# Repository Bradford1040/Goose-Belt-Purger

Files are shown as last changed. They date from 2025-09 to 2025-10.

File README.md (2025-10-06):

# Goose Belt Purger (GBP)
A simple, lightweight, and low-cost belt purger for 3D printers.\
An alternative to blob-producing purging routines and devices, or traditional purging into towers.\
Officially supported printers are Voron Trident and 2.4, but it is small and light enough to be adapted for other printers.

   
  
See also our [promo video](https://youtu.be/ZBZhAEFlKdA) on YouTube, or slightly older [video](https://youtu.be/MWTFuGqhi_c) with more detailed depiction of purger in action.
  
Currently in Beta testing — proven as a functional design, but can have unexpected issues and design might change any time.  
  
If you have any questions, you can visit my [Discord server](https://discord.gg/8a29q9gJb9).  
  
If you find this useful, a like or a make on [Printables](https://www.printables.com/model/1371713-goose-belt-purger-gbp) helps others discover and trust the design.

# About
Like many makers, I've been fascinated by single-nozzle multicolor/multimaterial printing. But like many, I hate purge towers. They can be large, ugly, and take up valuable print bed space. This is why I was intrigued by the Blobifier — but there are several issues. First, I use a Voron Trident, which isn't compatible. While there are adaptations of the Blobifier concept for the Trident, none have gained significant traction. Second, both the original Blobifier and its Trident adaptations generally share the drawback that each purge requires toolhead parking near the bed edge, blocking part of the bed and potentially risking collisions. Third, the produced blobs are volumetrically inefficient. Even though the blobs are relatively compact, their shape means they can't utilize the waste bin space effectively. This is even worse with the loose coil "poops" produced by some printers.

There had to be a better way.

And then it struck me — use a belt to produce compact "line" purges. To be fair, this isn't an entirely new idea. There have been mods involving purging on stationary aluminum platforms or kinematic belts, but none of those options felt right. I wanted something simple, affordable, and buildable from stuff you already have lying around your workshop.\
This is why the Goose Belt Purger was created.

What does it have to do with geese? Nothing. I just like geese.

# Design

The core of the GBP is a silicone wristband — the kind you can get anywhere, often for free. The most common size, which GBP is designed around, is 12 mm wide and 20 cm in circumference. You can use any similar band, even ones with embossing or printing, since we'll use the smooth inner surface. Changing the belt is easy, so use whatever you have and swap it later if needed.

Silicone rubber is ideal for this use. When filament is extruded onto the smooth side, it sticks but releases easily at the end of the straight belt section. Silicone is heat-resistant enough to endure the nozzle heat, provided it keeps moving. However, if the nozzle stays in one place too long, the band will discolor (brown or black) or even burn.

The belt moves along two printed pulleys. How does it stay in place without flanges? Dark magic. Don't ask.

One pulley is driven by a cheap miniature DC motor with a gearbox.  A 50rpm or slower version is recommended, up to 15rpm if you want really thick extrusions. &#x20;

> [!WARNING]\
> Motor is an inductive component. Skipping the recommended protection (e.g. flyback diode) can cause voltage spikes and permanent damage to your controller.  
>  
>Read the “Electrical connection” section and install all safety components.  
>Use at your own risk.  

The other pulley spins freely on a tilting arm. The arm pivots on a bearing around the motor shaft and is pushed upward by a pair of magnets acting as springs. The arm's purpose is to press against the nozzle but move away to avoid collisions with the nozzle or printhead.

GBP is mounted using an Armored Turtle brush mount or universal Klicky style mount. But you can also design your own mount and connect it with AT mount styled dovetails.

# Bill of Materials (BOM)
## Purger
- 1x Silicone wristband (12 mm wide, 200 mm circumference)
- 1x DC motor, 12 mm diameter, 6V/12V, 15rpm — commonly sold as GA12 N20 or N30. See note below.
- 3x 623 bearings
- 2x 6x3 mm magnets (Voron standard size)
- 3x heat-set insert M3x5x4 (Voron standard size)
  
If your board supports 5V on fan outputs, you may use a 6V motor. If only 24V is available, use a 12V motor with <50% PWM.  
Initial testing shows optimal belt speed under load is 2–12rpm, so the 15rpm seems to be ok. PWM can reduce speed to \~5–10% of rated speed. 30rpm and 50rpm motors also seem to be usable  

**M3 hardware:**

- 1x M3 nut
- 1x M3 nylock nut*
- 1x M3x6 set screw
- 1x M3x20 SHCS*
- 2x M3x20 FHCS
- 1x M3x30 SHCS
  
*) If you have trouble getting a M3 nyloc, you can instead use HSI variant of arm - replace nylock nut for one more heat-set insert, M3x16 SHCS instead of M3x20 SHCS and get some threadlocker  

**Electrical components:**
- Schottky diode 1A (e.g. 1N5819) - For 5V or 12V supply voltage  
or
- Schottky diode 2A (e.g. 1N5820) - For 24V supply voltage together with 12V motor  
- Resistor 47R
- Ceramic capacitor 10 nF, 50V 
  
If you don't like the idea of soldering those parts, you can also get yourself a **[MicroFlip](https://github.com/Trondle-Embeeded-Systems/MicroFlip)** board, which already has everything.

## Mounts
**AT mount**  
Applies to Voron Trident or similar printer together with modified (shorter) AT mount files  
- 2x heat-set insert M3x5x4 (Voron standard size)
- 2x M3 nyloc nut
- 2x M3x8 SHCS
- 1x M3x35 SHCS (you can use M3x30 if you have trouble getting it)
- 1x M3x25 SHCS

**Klicky style mount**  
Universal solution  
- 8x heat-set insert M3x5x4 (Voron standard size)
- 8x M3x8 SHCS

# Build Instructions

Build instructions can be found [here](assembly.md).

# Electrical Connection

Connect the DC motor to any free power output on your controller board, preferably a fan output. If possible, supply it with 5V or 12V to minimize heating. Otherwise, reduce voltage via PWM.

> [!IMPORTANT]\
> The DC motor is a strong inductive load and will generate large voltage spikes, which can destroy your board's MOSFET or even the MCU if untreated. At minimum, use a properly sized Schottky flyback diode across the board output. I also recommend an RC snubber on the motor terminals.
>
> Some boards (e.g., BTT Octopus) already include protection diodes. Others rely only on the MOSFET's internal diode, which is usually insufficient. You can check comprehensive table [here](board_list.md), or consult your board's schematic.  When unsure, ask someone.
>
> For the RC snubber, I used a 47 Ω resistor and a 10 nF, 50V ceramic capacitor. Solder one leg of each component together, then solder the free legs to the motor terminals. This configuration dampens voltage spikes while preserving PWM response. You may use a larger capacitor for extra safety, but note that increased capacitance degrades PWM response. Avoid using a capacitor alone (without resistor), as this can cause resonance and make things worse.

I confirmed the effectiveness of these measures with an oscilloscope, but I can't guarantee that no fast transients were missed (e.g., during PWM changes). Data is still limited, so proceed with care and understand what you're doing.

If you want some better alternative to manually soldering components to motor, see amazing [MicroFlip](https://github.com/Trondle-Embeeded-Systems/MicroFlip) project by Ntrondle. You can make it yourself, or check our Discord if anyone has any boards for sale. Keep in mind, that MicroFlip is **not** developed as part of this project. If you like it and would like to support its creator, do so on his GitHub page.  

# Software and Slicer Configuration
For more information about provided configuration file, slicer configuration and integration into AFC or Happy Hare, please look [here](sw_configuration.md).

# Tips and Observations
 
Extrude onto the smooth inner side of the wristband. You can try the outer side, but adhesion is generally worse and requires an unembossed, unprinted band — which is surprisingly hard to find. The inner surface sticks well, even without direct nozzle contact, while the outer side requires pressure that magnets alone can't provide.

Adhesion heavily depends on belt speed. If filament doesn't stick, slow the belt. Once adhesion starts, the extruded line tends to pull more material from the nozzle. 
  
Adhesion is also strongly dependant on filament drynes. Wet filament tends to curl up and does not stick to belt as easilly.

The macro splits the purge into short "toothpicks" or pellets to improve waste volume efficiency.

Initial testing shows optimal belt speed is 2–12rpm (roughly 1.8–11 mm/s or 108–660 mm/min). The easiest way to measure speed is to mark a spot on a pulley, start a stopwatch, and time 10 full revolutions.

Don't be afraid to experiment with the macro parameters. Every printer is unique, so expect to tune it up for a some time untill you hit the 'just right' zone.

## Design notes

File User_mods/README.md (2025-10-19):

#Goose Belt Purger - User mods
Files in this folder are user mods related to the Goose Belt Purger. Although they have been curated by me (Graylag) and have been confirmed to meet certain minimum standards, they are not considered a core part of the project and are neither developed nor maintaned by the GBP team.  
All credit goes to the original authors of these mods. If you have any questions or ideas, please try to contact the original authors. Our Discord server might be an ideal place to do that.  
  
Would you like to have your mod here? Contact me on Discord (username graylag) or send me an email. I reserve the right to not publish every submission, but if your work meets minimum qzality requirements and can be helpful to someone, I will try to publish it.  

##List of the user mods

Dragi2k's alternative V2.4 mount - by Dragi2k

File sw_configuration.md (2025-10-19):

# Configuration file and macro configuration
Applies to configuration file v0.7.1 or newer. If you have any kind of issues, check first, if you are on newest available version.

## Instalation of macro into Klipper
Copy the `goose_belt.cfg` file into Klipper configuration file and add `[include goose_belt.cfg]` into your `printer.cfg`. No additional steps are needed

## Macro configuration
Macro can be configured by changing its user accessible variables. See comments in the file and adapt it to your printer.  

Once set up, the purge routine can be triggered by running the G-code macro:  
 - `GOOSE_PURGE PURGE_VOLUME=###`  
   or  
 - `GOOSE_PURGE PURGE_LENGTH=###`  
where ### is the purge volume in mm³ or length in mm. If both are provided, PURGE_LENGTH takes precedence. If neither is provided, the macro runs according default value variable configured within the macro.

## Useful tips
Tuning the variables "just right" can take many iterations and hitting that Save&Restart button every time can be very time consuming. Instead, you can edit your variables on the fly through terminal command `SET_GCODE_VARIABLE`, e.g. `SET_GCODE_VARIABLE MACRO=goose_purge VARIABLE=belt_pwm VALUE=0.33` to change the belt speed. You can even do that during print job - set up a test print that has a bunch of filament changes, then adjusted the variables live as you go. Because the way klipper queues up gocode, it may not take effect immediately so if you enter this while you're in the middle of a toolchange, you won't see the results until the next toolchange.  
Keep in mind this doesn't save the values to config file, so you will have to remember to set the values in the cfg file yourself. 

## GBP and other printer firmwares
No other printer firmwares are supported as of this moment. We are open to add support for other firmwares if you are interested, however be prepared to provide extensive support for a development for your choosen platform.

# Integration of Goose Belt Purger into your print jobs

## Standalone operation (Slicer controlled)
You can use GBP in standalone mode independently on any other klipper add-ons. You can even use it this way if you don't have any MMU/AMS on your printer, e.g. for manual filament changes. Purging can be triggered manualy, or more commonly by slicer.  

Slicer configuration is following:  
For initial priming, place the `GOOSE_PURGE` command with appropriate parameter at the beginning of your **Start G-code** where you'd normally place a prime line.  
For tool changes, insert the command into **Tool change G-code** just after the `T#` command.  
Note that not all slicers support passing purge parameters. In OrcaSlicer, you can use `GOOSE_PURGE PURGE_LENGTH=[flush_length]`. In PrusaSlicer, the volume must be hardcoded.  For other slicers, consult their documentation. 

If you are using GBP in standalone mode but let filament changes handling to Happy Hare or a similar tool, configure it so it doesn't return toolhead to the previous or next G-code position to avoid unnecessary travel.  

## AFC integration 
*Contributed in full by adamcstorm*  
To integrate with AFC-Klipper-Add-On:  

Modify `AFC.cfg`. Under the Macro Config section, change the poop settings to use the goose_purge macro, and disable the kick option:  
```
# Poop Settings
poop: True                      # Enable Poop.
poop_cmd: GOOSE_PURGE           # Poop macro name.

# Kick Settings
kick: False                     # Enable Kick.
kick_cmd: AFC_KICK              # Kick macro name.
```
All other settings can be enabled/disabled per your preference.  
Of note, if you have wipe enabled, the wipe routine will be called twice. This is due to the default AFC order of operation that wipes both before and after the kick routine. Since we have disabled the kick routine, it performs the wipe twice in a row. It is recommended to disable the wipe option in `AFC.cfg`, and instead call the brush routine within the `goose_purge` macro by modifying the user_end_script variable: `variable_user_end_script: 'AFC_BRUSH'`.

GBP is compatible with the default AFC method of passing the variable purge length from the slicer to the print via gcode. To configue this, follow this guide:  
https://www.armoredturtle.xyz/docs/afc-klipper-add-on/features.html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.  
Be aware, that the GBP macro does not access the AFC variables and as such ignores the AFC's variable `variable_purge_lenght`. Instead you should configure GBP's own variable `variable_default_purge_volume`. This value gets used only when no purge parameters are provided, such as during initial load. 

## Happy Hare integration
Happy Hare takes rather complex approach to purging. Unlike other methods it does not rely on slicer to pass purge volume or length together with toolchange. Instead it works with internal purge volume matrix and further enhances it by adding volume of residual filament and cut tip fragment. It can get its purge volume matrix either from internal toolmap or from processing gcode metadata. Either way, for purging to work you need to make sure, that your instance of Happy Hare processes this data correctly. For more information, please visit Happy Hare documentation here:  
https://github.com/moggieuk/Happy-Hare/wiki/Tip-Forming-and-Purging

Also please note, that even if your Happy Hare is configured correctly, it relies on slicer to pass the purging matrix correctly. While this assumption seems to be met for Prusa Slicer, it does not seem so for Orca Slicer. If you use Orca Slicer, consider generating purge volume matrix from toolmap, using custom purge volume matrix or operating GBP in standalone mode.  

As for actual integration, this is very straightforward and the only thing you need to do is edit `mmu_macro_vars.cfg` by setting variable `variable_user_post_load_extension : '_GOOSE_PURGE_HH'` without any parameters.   
  
Note, that we are not calling directly `GOOSE_PURGE` macro, but instead its wrapper `_GOOSE_PURGE_HH`. This is due to how Klipper resolves macros and passes parameters.
  
Happy Hare does not have any wiping logic embedded, so if you want automatic wiping execution after purge, consider adding your custom wiping macro to the `variable_user_end_script:''` in `goose_belt.cfg`.

## Other filament management add-ons
No other filament management add-ons are supported as of this moment. You are free to develop integration into other add-ons and if you do, we can list them here, however be prepared to support such solution.

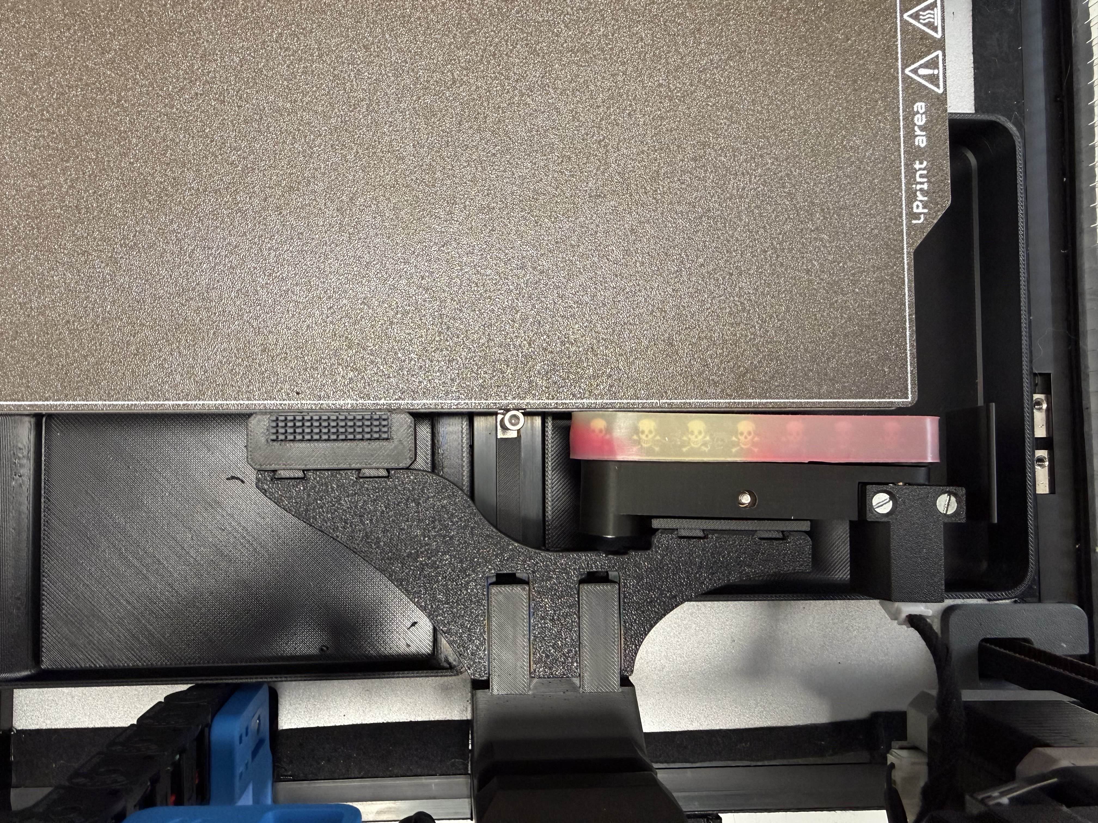
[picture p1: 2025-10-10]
Assets/V2.4/image.jpg

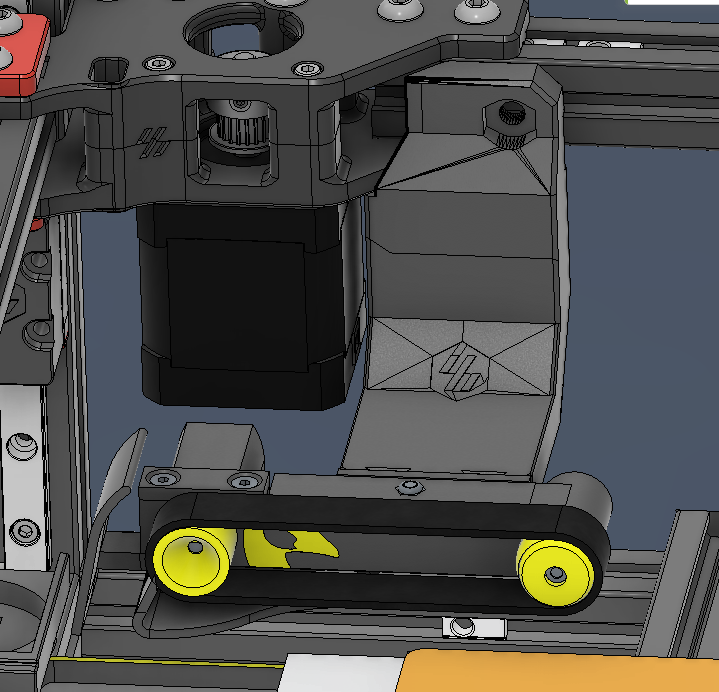
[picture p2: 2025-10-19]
User_mods/Dragi2ks_alternative_v2.4_mount_-_by_Dragi2k/image.png

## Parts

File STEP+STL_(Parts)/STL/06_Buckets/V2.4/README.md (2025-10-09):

Center - to be placed in between bed profiles. It is supposed to catch debris from the brush  
  
Front access - Bucket shaped in such way, that it can be slid under the bed all the way to the front and pulled out of printer. 
Can be removed without lifting the gantry, but does not have locking mechanism to frame. You can either leave it loose, or you can secure it with self adhesive velcro.

Rear access - Bucked designed to be removed by moving it towards back and lifting it along rear panel. Has locking to frame by clips, but requires to lift gantry high up before emptying.

Center bucket and Front access buckets were designed by AmfKuna

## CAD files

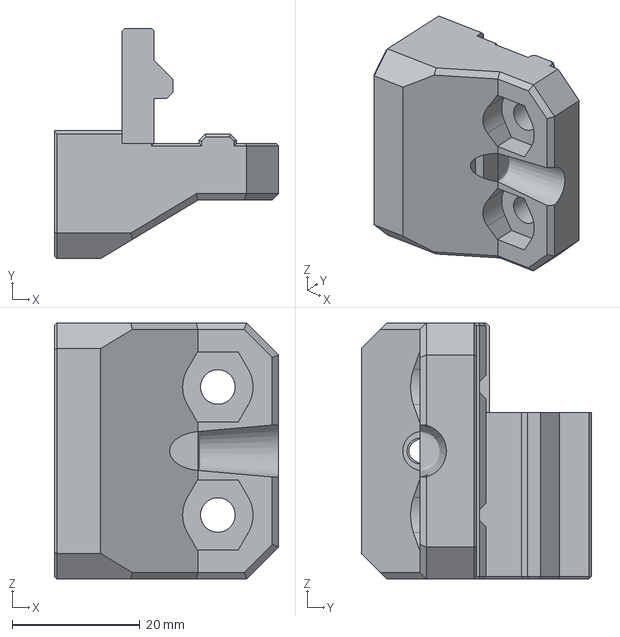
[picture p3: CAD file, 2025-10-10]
STEP+STL_(Parts)/STEP/01_Mounts/AT_Style-Voron_Trident+2.4/ATmount_upper_(GBP).step
35.0 x 36.0 x 40.0 mm

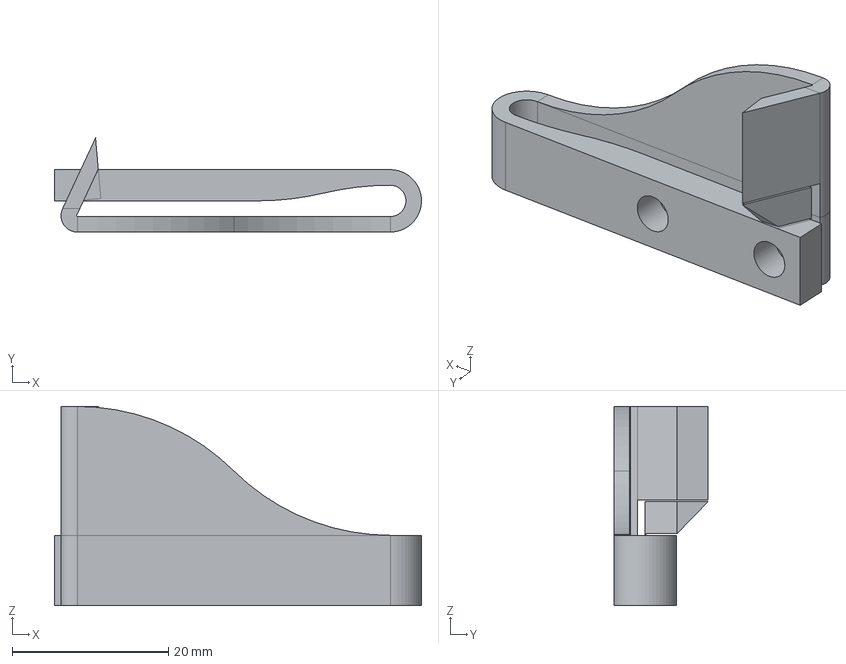
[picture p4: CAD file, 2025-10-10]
STEP+STL_(Parts)/STEP/02_Alternative_parts/GBP_Deflector_lite.step
47.0 x 12.1 x 25.5 mm

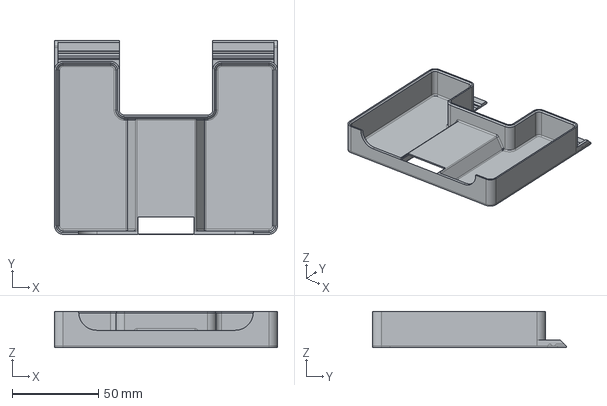
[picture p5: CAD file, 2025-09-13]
STEP+STL_(Parts)/STEP/04_Buckets/bucket_V2.4-central.step
129.0 x 112.0 x 21.0 mm

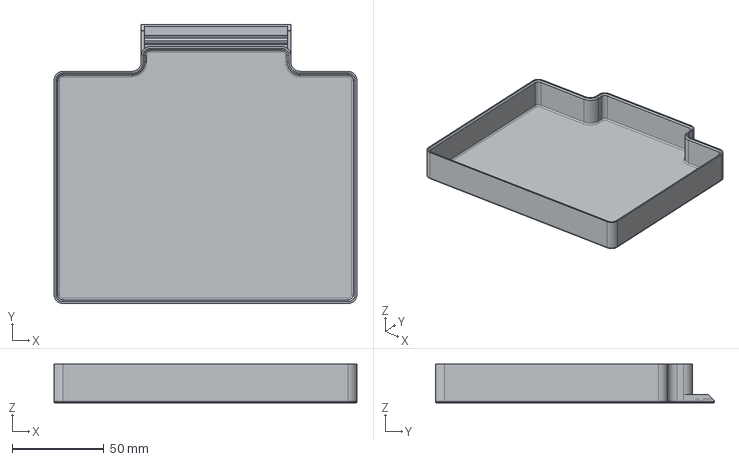
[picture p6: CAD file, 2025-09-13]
STEP+STL_(Parts)/STEP/06_Buckets/Trident/bucket_Trident-300.step
165.0 x 152.0 x 21.0 mm

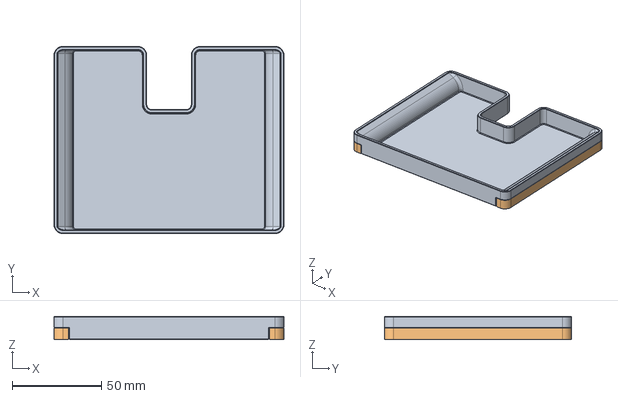
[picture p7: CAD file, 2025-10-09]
STEP+STL_(Parts)/STEP/06_Buckets/V2.4/V2.4_Center/GBP_V2.4-center_bucket.step
129.0 x 105.0 x 13.0 mm

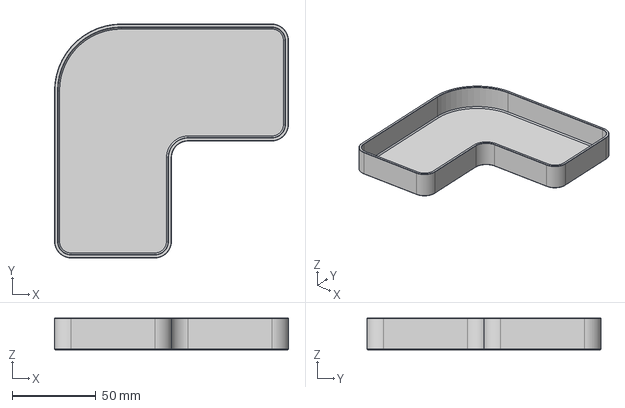
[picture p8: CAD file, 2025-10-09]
STEP+STL_(Parts)/STEP/06_Buckets/V2.4/V2.4_Front_access/GBP_bucket_V2.4-300.step
140.0 x 140.0 x 19.0 mm

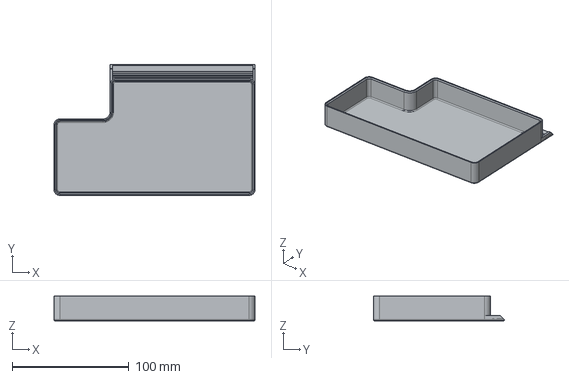
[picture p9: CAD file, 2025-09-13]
STEP+STL_(Parts)/STEP/06_Buckets/V2.4/V2.4_Rear_access/bucket_V2.4-350.step
172.0 x 112.0 x 21.0 mm

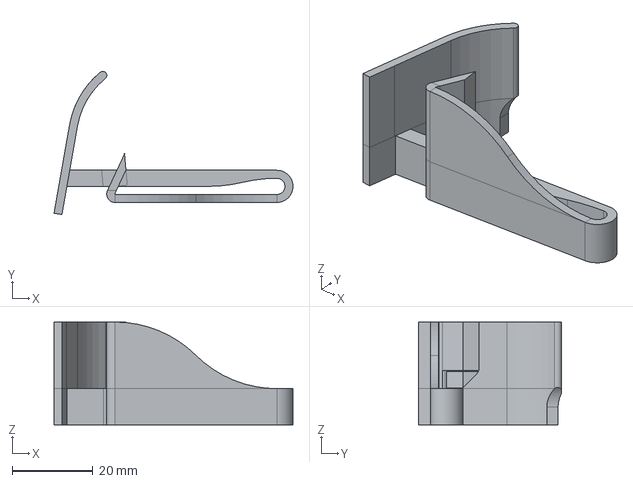
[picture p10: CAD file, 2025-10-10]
STEP+STL_(Parts)/STEP/GBP_Deflector.step
59.2 x 35.5 x 25.5 mm

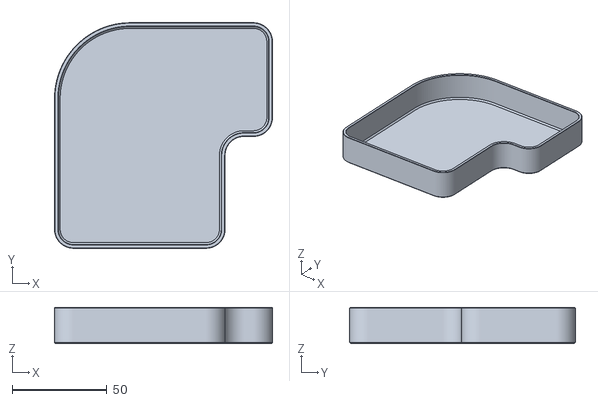
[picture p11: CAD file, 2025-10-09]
STEP+STL_(Parts)/STL/06_Buckets/V2.4/V2.4_Front_access/GBP_bucket_V2.4-250_front.stl
115.0 x 119.0 x 19.0

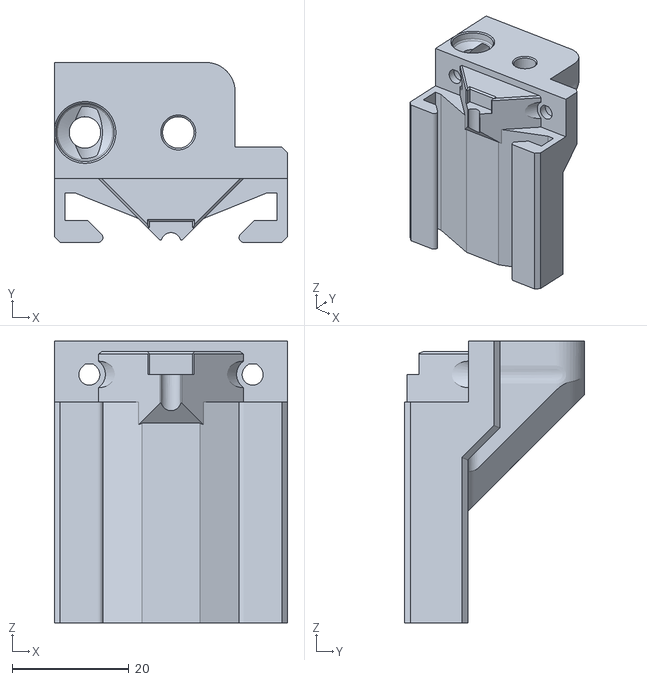
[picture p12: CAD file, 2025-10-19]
User_mods/Dragi2ks_alternative_v2.4_mount_-_by_Dragi2k/V2.4 AT mount side mod.stl
40.0 x 30.9 x 48.4

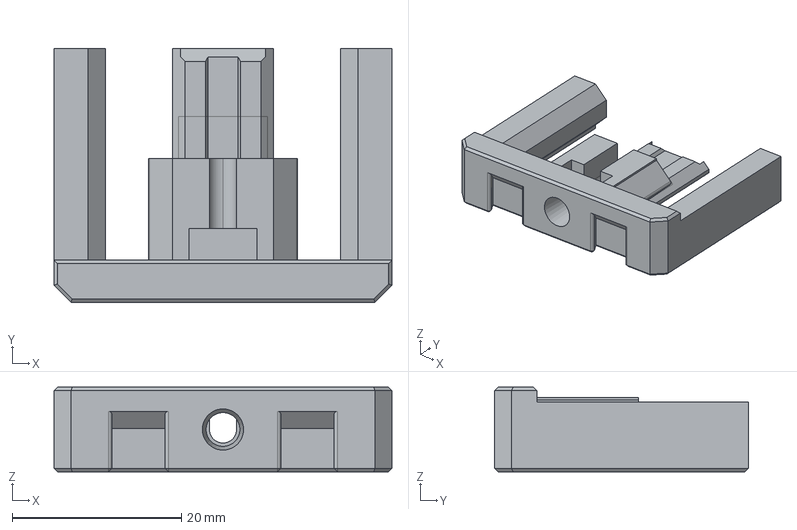
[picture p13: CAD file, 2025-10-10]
STEP+STL_(Parts)/STEP/01_Mounts/AT_Style-Voron_Trident+2.4/ATmount_front_arm_slide_(GBP).step
40.0 x 30.0 x 10.00 mm

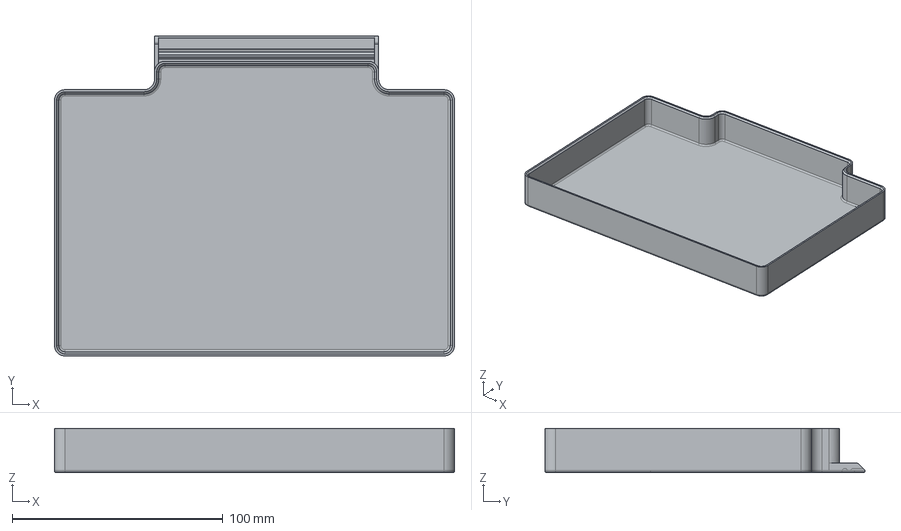
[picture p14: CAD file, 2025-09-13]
STEP+STL_(Parts)/STEP/06_Buckets/Trident/bucket_Trident-350.step
190.0 x 152.0 x 21.0 mm

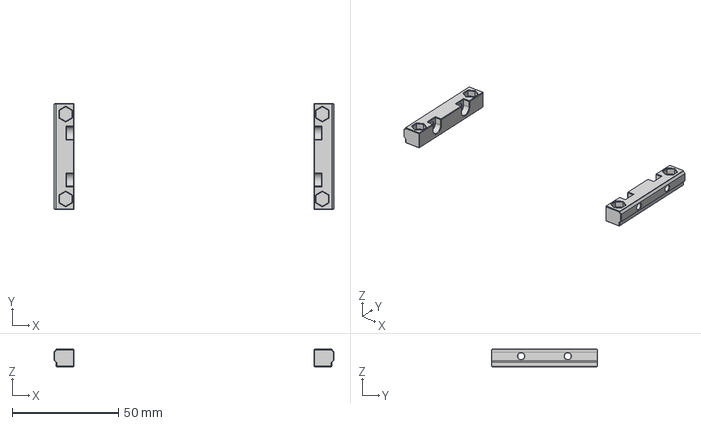
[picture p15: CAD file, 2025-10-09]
STEP+STL_(Parts)/STEP/06_Buckets/V2.4/V2.4_Center/GBP_V2.4-center_bucket_mounts.step
132.0 x 50.0 x 8.30 mm

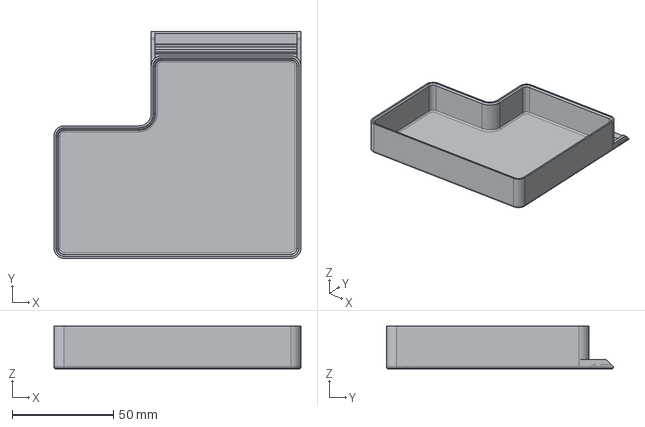
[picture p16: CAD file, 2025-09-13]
STEP+STL_(Parts)/STEP/06_Buckets/V2.4/V2.4_Rear_access/bucket_V2.4-250.step
122.0 x 112.0 x 21.0 mm

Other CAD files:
STEP+STL_(Parts)/STL/06_Buckets/V2.4/V2.4_Center/center_bucket.stl
STEP+STL_(Parts)/STEP/02_Alternative_parts/GBP_Deflector_lite_noinserts.step
STEP+STL_(Parts)/STEP/06_Buckets/V2.4/V2.4_Front_access/GBP_bucket_V2.4-250.step
STEP+STL_(Parts)/STL/06_Buckets/V2.4/V2.4_Center/center_bucket_mounts_x2.stl
STEP+STL_(Parts)/STEP/01_Mounts/AT_Style-Voron_Trident+2.4/ATmount_front_arm_base_(GBP).step
STEP+STL_(Parts)/STEP/01_Mounts/AT_Style-Voron_Trident+2.4/ATmount_front_arm_slide_Trident_offset.step
STEP+STL_(Parts)/STEP/01_Mounts/AT_Style-Voron_Trident+2.4/ATmount_front_arm_slide_V2.4_offset.step
STEP+STL_(Parts)/STEP/01_Mounts/AT_Style-Voron_Trident+2.4/ATmount_lower_(GBP).step
STEP+STL_(Parts)/STEP/02_Alternative_parts/GBP_Deflector_long_noinserts.step
STEP+STL_(Parts)/STEP/02_Alternative_parts/GBP_Deflector_short.step
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

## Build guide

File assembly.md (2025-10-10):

# Goose Belt Purger assembly

## Preparation steps
a) Identify, if your board has protective flyback diodes. You can check the comprehensive list [here](board_list.md),. If not or you are in doubt, you will have to add it yourself to motor terminals. At this moment there are no known boards with RC snubber integrated, so expect to add snubber either way.
  
  
_Example of BTT Octopus with Schottky diode on board_  
  
b) Install heatset inserts into **GBP_Idler** (1x) and **GBP_Deflector** (2x). If you want to use HSI variant arm, install insert also to **GBP_Arm_HSI** (1x). If you plan to use an AT style or Klicky style mount, you can also install inserts in those parts.  
c) Remove integrated support of **GBP_Deflector_(long/short)**. Grab the small bridging element in the middle with small pliers and remove it with twisting motion. It should easily and cleanly detach.   

## Assembly steps
1. _(Skip this step if you are using MicroFlip board. Instead just solder MicroFlip to your motor)_  
   Solder wires to the motor. If your board does not have sufficient protection, solder a schottky flyback diode and/or RC snubber to the motor terminals together with wires  
  **_1a._** Correct polarity of the motor is needed. Output shaft of the motor should be turning CCW (or CW if you printed mirrored version). If you can, test the polarity beforehand. In case the motor spins other way, switch the wires. If you are not adding flyback diode, you can reverse them later on in connector. If you are adding flyback, you will need to revert them directly on the motor.  
  **_1b._** Schottky flyback diode has a set polarity and you need to solder its cathode to the motor terminal where positive voltage (+) wire is connected. Cathode is usually marked with a colour stripe. Other end of diode shall go directly to the other motor terminal. Double check the polarity, because doing this wrong may overload and damage your control board.  
  **_1c._** RC snubber is formed of a capacitor and a resistor. One leg of each component shall be soldered together (in series) and other legs to the motor terminals (one resistor leg to one motor terminal, one capacitor leg to other motor terminal). RC snubber does not have set polarity and it does not matter which way around do you solder it.  
   
    
_Example of snubber; schematic of snubber with diode_
   
2. Insert the motor to a slot in **GBP_Frame**. It should fit tightly, but not deform the part. Depending on your gearbox configuration you may have some play in axial direction. Try to place your motor in such a way, that the face with output shaft  is as flush with frame as possible.  
3. Clamp the motor from top with **GBP_Motor_cover**, push through 2x M3x20 FHCS screws, add **GBP_Deflector** to bottom and screw it together.  
4. Insert two of the bearings and one magnet into **GBP_Arm**. Bearings should be inserted from flat side (one with logo on it). Polarity of the magnet does not matter. If it is too loose, you may fix it with a drop of glue, but this should generally not be needed. Magnets act as a spring pulling arm away from mount and as such are being pushed into a pocket.  
5. Put M3x30 screw through remaining bearing, add **GBP_Bearing_spacer** on screw, then push the screw through arm opening and second bearing. Set the third bearing flush into hole and screw on **GBP_Idler**. Idler has to be fully tightened against bearing, but has to move freely. Do not overtighten, as it can damage your bearings.    
6. Put other magnet into Frame. Make sure to orient it in such a way, that it will repulse the magnet in Arm, when they are faced aginst each other.  
7. Slide the arm on the motor shaft, through remaining bearing. Make sure the arm can freely move up and down and that it gets pushed away from frame by magnets. Place nyloc nut to slot on top of arm _(does not apply to HSI variant)_ Secure the arm to mount with M3x20 SHCS _(M3x16 SHCS for HSI variant)_ screw (do not fully tighten). 
8. Push the M3 nut into a slot in **GBP_Motor_pulley** and screw in a set screw. You may need to push a nut deep inside with a screwdriver.  _Some users skip this step. This is ok, but can lead to pulley wobbling_
9. Push the pulley into the motor shaft. Push it as far as you can, but leave a tiny gap so that the arm is free to move. Tighten the set screw against motor shaft.  
10. Take the wristband, turn it inside out, slightly stretch it by hand and slide it on the pulley and idler. You don't need to put it into any specific position, it will self align when switched on.  
11. Test the assembly. Verify, that the motor turns when powered, that the arm can move and that the belt keeps turning without slipping off the pulleys. 

## Mount assembly and integration into printer
Purger is designed to be compatible with ArmoredTurtle brush mount and regarding its assembly, you should refer to AT's wonderful manual located [**here**](https://www.armoredturtle.xyz/manual.html?manual=at_brush&step=1)  
Alternatively you can use Klicky style mount, which lacks ease of operation of the AT brush mount, but can be easier to adapt for certain printers.  
  
Purger itself is connected to its mount via a dovetail connection. If your printer is properly tuned, GBP should mate with the mount firmly, without any residual movement, but also without the need for excessive force to mate them. If they are too hard to assemble, you can gently sand the sides of the dovetail wedges on the frame. If they are too loose, you can shim the purger with a piece of paper or thin plastic placed between the purger's frame and the AT mount.    
  
Once everything is in place, you can adjust the purger to the right position using screws in the AT mount. If you use the basic (not offset) mount, the horizontal adjustment screw gets exposed when you remove the vertical adjustment screw and lift the arm up. Don't forget to put this screw back once you are done.  
You should adjust the Z position so that that there is a tiny gap between the nozzle and the wristband. You can use the M3x20 SHCS screw for fine adjustment.  
In case you choose the HSI arm variant, you should secure your screw with threadlocker or any other means. If you don't, your screw will eventually fall out due to vibrations.

For instructions on how to use the mounts for the most popular printers, see below
  
### Voron Trident
For the Voron Trident you can use either a basic mount (without brush), or an offset version with a brush. The offset version is recommended, because it shifts most of the purger away from the bed, preventing collisions with any other mods you might have. If you decide to use a basic mount, keep in mind you have to use customized parts designed for GBP, which are 10 mm shorter than the stock AT brush mount parts.  
You can place your mount and purger anywhere you want as long as you don't have a collision with your bed. The intended position is as far to the left (or to the right for the mirrored version) as possible.

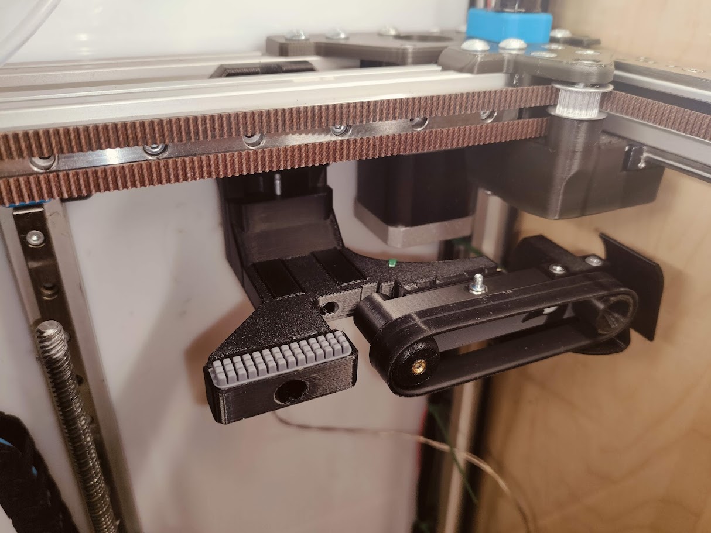
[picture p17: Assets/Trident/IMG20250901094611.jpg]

  
### Voron 2
For the Voron 2 you have to use a specifically designed offset mount, which clears the purger from colliding with the bed profiles. You are supposed to place the mount directly above the bed profile, so that the purger is on the left side of the printer (or right for the mirrored version) and the brush is in the center. In the case of the 250 mm frame size this will put the purger's end very close to the printer side panel, so you can consider using the "lite" version of the deflector, since the pellet guiding cover is effectively not needed.  
If you plan to use a waste bucket, make sure to mount it in your printer at this phase, to ensure you have enough clearance. 

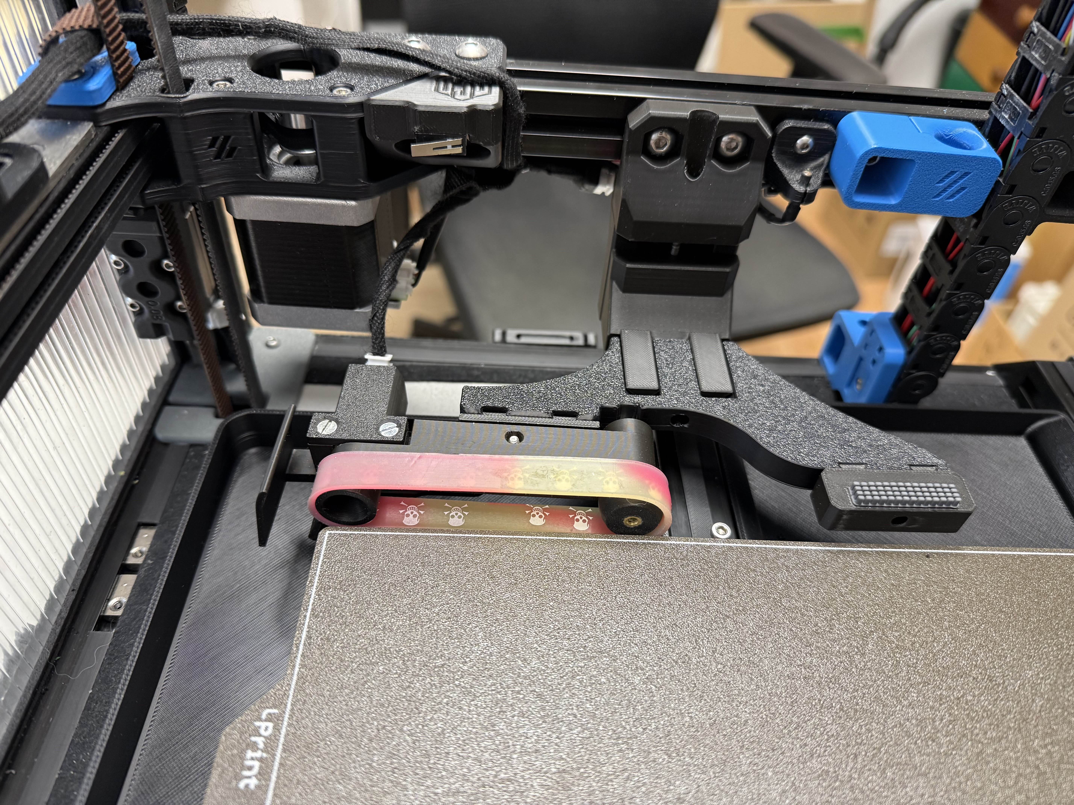
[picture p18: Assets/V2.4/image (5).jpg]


## Troubleshooting and FAQ
- My wristband shifts partially/fully off the pulleys towards bed - this is most likely due to bad tolerance of a bearings holding the idler and/or missing M3x16 SHCS screw. Some cheaper bearings allow the idler or arm to be pulled to the side by a band tension, which causes this shifting off. If you can, use a better bearing. Otherwise try using **GBP_Idler(+3,0)**  
- My wristband shifts too far in, towards motor - less common, could be due to arm being warped. Try using **GBP_Idler(+0)**

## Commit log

2025-09-11 bucket ab01
    [bucket_V2.4.step, frame_clamp.step]
2025-10-09 a012 part 2
    [ATmount_front_arm_slide_V2.4_offseted.step, GBP_V2.4-center_bucket.step, GBP_V2.4-center_bucket_mounts.step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]
